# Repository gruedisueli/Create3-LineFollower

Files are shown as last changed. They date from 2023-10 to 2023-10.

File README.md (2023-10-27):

# Create3-LineFollower

This codebase enables the use of the Create3 with Sparkfun's Line Follower Array (SEN-13582). [This is the product](https://www.sparkfun.com/products/13582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) we are using in this project.

We also used an [Arduino Nano IoT](https://store.arduino.cc/products/arduino-nano-33-iot), connected to the iRobot's USB port, but any device that uses 3.3v logic but offers a 5v power output should be sufficient. The line-follower array depends on 3.3v logic but requires 5v power.

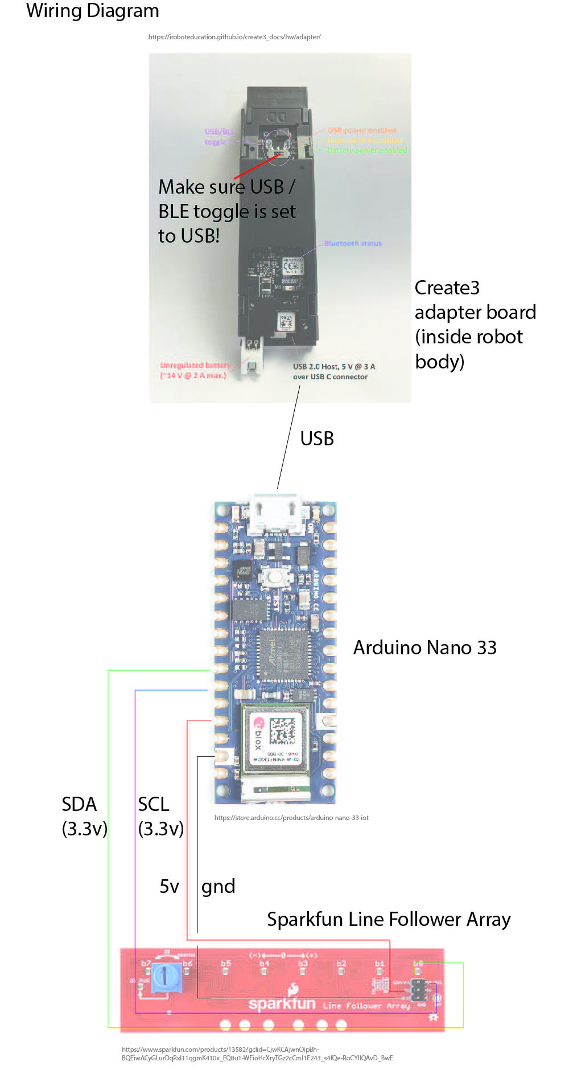
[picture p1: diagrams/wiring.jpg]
Here's the wiring diagram


## General control system:
1. The line-follower array sends data to the Arduino
1. The Arduino processes this and performs some data smoothing and analysis
1. The final position information is forwarded over USB serial to the Create3
1. The Create3 forwards this data over wifi/port without performing additional processing
1. An external CPU listens to data coming from this port
1. The external CPU processes the data and determines if the robot should turn, etc
1. The external CPU sends commands to the Create3 using ros2

## Limitations:
1. Currently the robot can only drive backwards, because of where the sensor is located (underneath the robot, behind the wheels), and this means that the ros2 scripts must override the safety system of the Create3 that limits backwards driving. We are interested in developing a forward-mounted sensor and may add this in the future.
1. Depending on the floor color, you will have better or worse outcomes. The line-follower array is extremely sensitive to contrast and lighting. We had better results using the sensor in "inverted" mode, where it detects a while line on a dark background. This seemed to be more versatile with different floor types
1. Floor smoothness affects accuracy of readings, since as the robot drives over bumps the line on the ground will vary in distance.
1. The Create3 has a minimum speed, and that is the speed we are specifying in our scripts.

## Ros2 Installation, Create3 setup, tutorials:
1. Refer to instructions in my other repository [here](https://github.com/gruedisueli/Create3-Grasshopper-Toolkit)

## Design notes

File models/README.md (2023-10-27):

# 3d Printable Models
Here you will find both Rhino (.3dm) and STEP files that can be printed.

The 3d printable tray consists of some sub-elements
1. The main tray, broken into subunits to print faster:
    1. The large part
    1. A horizontal plate to cover the big hole in it
    1. A part to hold the Create3's metal ballast, printed separately to ease cleanup of printed file.
    1. A separate bracket that is designed to fit the Sparkfun Line Follower Array.

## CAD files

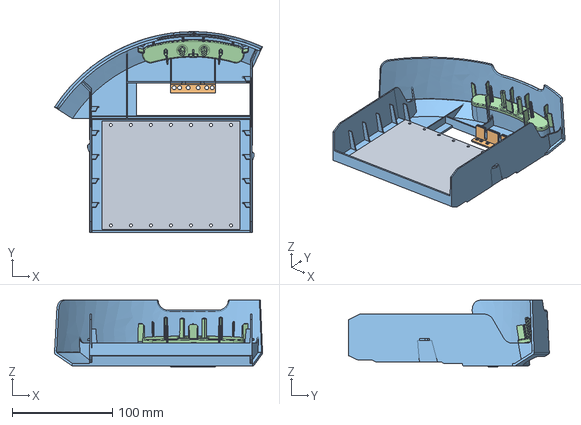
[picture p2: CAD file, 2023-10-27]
models/Tray.stp
207.7 x 200.5 x 66.4 mm

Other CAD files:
models/Tray.3dm

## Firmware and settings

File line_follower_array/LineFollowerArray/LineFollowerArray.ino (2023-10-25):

//WE HAVE ADAPTED SPARK-FUN'S CIRCULAR BUFFER EXAMPLE TO MEET OUR NEEDS ORIGINAL LICENSE BELOW
//We take the averaged positon and transmit over the serial connection
//We tested this on an Arduino Nano IoT
//The nano should be plugged into the USB connection of the Create3 adapter board.
//Follow iRobot's instructions for configuring serial communications. 
//Make sure that the Bluetooth/USB switch on the adapter board is on the "USB" setting



/******************************************************************************
AveragingReadBarOnly.ino

A sketch for reading sensor data into a circular buffer

Marshall Taylor, SparkFun Engineering

5-27-2015

Library:
https://github.com/sparkfun/SparkFun_Line_Follower_Array_Arduino_Library
Product:
https://github.com/sparkfun/Line_Follower_Array

This sketch shows how to use the circular buffer class to create a history of
sensor bar scans.
The buffer configured with CBUFFER_SIZE to have a length of 100 16bit integers.

Resources:
sensorbar.h

Development environment specifics:
arduino > v1.6.4
hw v1.0

This code is released under the [MIT License](http://opensource.org/licenses/MIT).
Please review the LICENSE.md file included with this example. If you have any questions 
or concerns with licensing, please contact techsupport@sparkfun.com.
Distributed as-is; no warranty is given.
******************************************************************************/
#define CBUFFER_SIZE 100
#define DEBUG false

#include "Wire.h"
#include "sensorbar.h"

// Uncomment one of the four lines to match your SX1509's address
//  pin selects. SX1509 breakout defaults to [0:0] (0x3E).
const uint8_t SX1509_ADDRESS = 0x3E;  // SX1509 I2C address (00)
//const byte SX1509_ADDRESS = 0x3F;  // SX1509 I2C address (01)
//const byte SX1509_ADDRESS = 0x70;  // SX1509 I2C address (10)
//const byte SX1509_ADDRESS = 0x71;  // SX1509 I2C address (11)

SensorBar mySensorBar(SX1509_ADDRESS);

CircularBuffer positionHistory(CBUFFER_SIZE);


void setup()
{
  Serial.begin(115200);  // start serial for output

  #if DEBUG
  Serial.println("Program started.");
  Serial.println();
  #endif
  
  //For this demo, the IR will only be turned on during reads.
  mySensorBar.setBarStrobe();
  //Other option: Command to run all the time
  //mySensorBar.clearBarStrobe();

  //Default dark on light
  //mySensorBar.clearInvertBits();
  //Other option: light line on dark
  mySensorBar.setInvertBits();//USE LIGHT ON DARK; IT'S GENERALLY MORE RELIABLE UNLESS YOU HAVE A BLACK LINE ON A VERY BRIGHT BACKGROUND.
  
  uint8_t returnStatus = mySensorBar.begin();
  if(returnStatus)
  {
    #if DEBUG
	  Serial.println("sx1509 IC communication OK");
    #endif
  }
  else
  {
    #if DEBUG
	  Serial.println("sx1509 IC communication FAILED!");
    #endif
	  while(1);
  }
  #if DEBUG
  Serial.println();
  #endif
}

void loop()
{
  delay(25);//don't overload the Create3 with messages.

  //Get the data from the bar and save it to the circular buffer positionHistory.
  int temp = mySensorBar.getDensity();
  if( (temp < 4)&&(temp > 0) )
  {
    positionHistory.pushElement( mySensorBar.getPosition());
  }

  //send values over serial to Create3
  
  int16_t i;
	//Get an average of the last 'n' readings
  int16_t avePos = positionHistory.averageLast( 10 );
  //values may be beyond normal signed 8bit range, but valid ones are -127 to 127
  //we can clamp it.
  int16_t clamped = constrain(avePos, -127, 127);
  int16_t shifted = clamped + 128;
  uint8_t bytePos = (uint8_t)shifted;//unsigned value for simplicity on the receiving end in ros2
  Serial.write(bytePos);

  //YOU CAN UNCOMMENT THIS CODE OUT (BELOW) IF YOU WANT TO SEE SPARKFUN'S METER
  //THIS ONLY WORKS IF YOU CONNECT THE ARDUINO DIRECTLY TO YOUR COMPUTER RATHER THAN CREATE3, BUT IS GOOD FOR DEBUGGING
  //   Serial.print("Scale = 5/char :");
  //   for( i = -130; i <= 130; i = i + 5 )
  //   {
  //     if( i < 0 )
  //     {
  //       //if avePos within 5 of i
  //       if((avePos > (i - 3)) && (avePos <= (i + 2)))
  //       {
  //         Serial.print("*");
  //       }
  //       else
  //       {
  //         Serial.print("-");
  //       }
  //     }
  //     else if( i == 0 )
  //     {
  //       //if avePos within 5 of i
  //       if((avePos > (i - 3)) && (avePos <= (i + 2)))
  //       {
  //         Serial.print("*");
  //       }
  //       else
  //       {
  //         Serial.print("+");
  //       }
  //     }
  //     else if( i > 0 )
  //     {
  //       //if avePos within 5 of i
  //       if((avePos > (i - 3)) && (avePos <= (i + 2)))
  //       {
  //         Serial.print("*");
  //       }
  //       else
  //       {
  //         Serial.print("-");
  //       }
  //     }
  //   }
  //   Serial.print(" avePos = ");
  //   Serial.println(avePos);
  
}

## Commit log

2023-10-27 added documentation and models
    [Tray.3dm, Tray.stp]
2023-10-27 update wiring diagram
2023-10-27 remove wiring diagram
2023-10-27 add wiring diagram
